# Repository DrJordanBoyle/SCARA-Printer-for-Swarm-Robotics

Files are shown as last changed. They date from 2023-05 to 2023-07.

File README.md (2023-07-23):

# SCARA-Printer-for-Swarm-Robotics
The project explores the development of compact mobile 3D printers inspired by the collective behavior of termites. By mimicking the swarm-like construction techniques employed by termites, this research aims to revolutionize the construction industry through the implementation of innovative robotic systems.
ASS Robotic-Builder_2023-May-10_05-36-22PM-000_CustomizedView9240691610_png_alpha

## Key Points:

1. Termites as Inspiration: Termites exhibit remarkable cooperative behavior in constructing intricate structures without a centralized control unit. Drawing inspiration from this, the project seeks to leverage swarm robotics to enhance construction processes.

2. Compact Mobile 3D Printers: The project has successfully designed and built compact mobile SCARA printers capable of delivering high-quality prints at a relatively high speed. These printers offer the advantage of mobility and flexibility in various construction scenarios.

3. Voxel Printing Strategy: The research introduces a novel voxel printing strategy, simplifying the printing process and increasing efficiency. The proposed strategy has been tested and demonstrated its potential for real-world applications using the SCARA printers.

4. Use Cases and Implications: Swarm 3D printing with SCARA robots holds significant potential in various construction domains. It can streamline building construction, aid in disaster relief efforts by rapidly constructing temporary shelters, and contribute to the expansion and modification of existing structures.

5. The project's findings pave the way for further advancements in swarm robotics and additive manufacturing, providing new possibilities for the construction industry. The research showcases the exciting potential of compact mobile 3D printers and their ability to transform construction processes. This project's outcomes contribute to a safer, more efficient, and sustainable future for the construction sector.

## Navigating the folders:
- In the "Hardware" folder you will find assembly instructions and the .STL files for the 3D printed components.
- In the "Firmware" folder you will find a small log that describes the adjustments made to the standard Marlin firmware and also the custom firmware itself.
- Please use the github in combination with the Thesis paper to fully understand the concept! The thesis 
"Design of a compact and mobile 3D Printer" can be found using the following link: https://repository.tudelft.nl/islandora/object/uuid:e90902cd-7b72-4dd6-bcc3-7ea3ccd2e8e0

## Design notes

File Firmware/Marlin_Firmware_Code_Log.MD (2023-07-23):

# Marlin Code Log

In this segment information is given in regards to what alterations were done to the original Marlin code to have the machine up and running. Good to note is that some changes may have been undocumented. I have tried to add comments to every adjustment, but only wrote them down at the end. It was a long process, you may find an altered line of code that is not documented in this file! You can contact me to update the document. General information on how to work and compile Marlin firmware can be found online. The motherboard we used was generally used to upgrade Creality machines, so some specific adjustments needed to be made. But again, this information can be found online :)

- Marlin version 2.0.9.5
- BTT SKR Mini E3 V3.0 motherboard
- E3D V6 Hot end

## Files that have been altered

- Configuration.h
- scara.cpp

## Configuration.h

- #define MOTHERBOARD BOARD_BTT_SKR_MINI_E3_V3_0 // Line ~90, adjust to own motherboard
- Line ~101 // adjust SERIAL_PORT to your motherboard’s settings
- Line ~114 // adjust BAUDRATE to your motherboard’s baudrate settings
- Line ~154-155 // SCARA_CROSSTALK_FACTOR and SCARA_IS_RIGHT_HANDED variables added to be able to work with different mechanisms. This system does not use an intermediate pulley and is right handed. Its full function can be found in scara.cpp.

#define SCARA_CROSSTALK_FACTOR 1

#define SCARA_IS_RIGHT_HANDED 1

- Line ~157 // define MP_SCARA to be able to use SCARA specific commands and functions
- Line 210-221 // Adjust driver type to the ones your system uses, our motherboard has integrated TMC 2209 drivers.
- Line 562 // Adjust temp_SENSOR_0 to the correct thermistor (we have E3D)
- Line 1098 // Adjust the DEFAULT_AXIS_STEPS_PER_UNIT depending on each stepper’s resolution and micro stepping settings.
- Line 1147-1164 // Some jerk settings were adjusted based on SCARA systems found online
- Line 1590-1601 // Bed dimensions and end stop positions were adjusted. Currently the safe working space is at X = 200 mm and Y = 60 mm. The current home position is set to the corner, but is not used at all in the current operation.

## Scara.cpp

- Line 35 // SCARA_CROSSTALK_FACTOR function added that changes it to 0 if not defined
- Line 56-65 // Forward kinematics were adjusted to include the crosstalk factor, some other older forward kinematics can be found in the file.

```
void forward_kinematics(const_float_t a, const_float_t b) {
  
    const float a_sin = sin(RADIANS(a)) * L1,
                a_cos = cos(RADIANS(a)) * L1,
                b_sin = sin(RADIANS(b + a * SCARA_CROSSTALK_FACTOR)) * L2,
                b_cos = cos(RADIANS(b + a * SCARA_CROSSTALK_FACTOR)) * L2;

    cartes.x = a_cos + b_cos + scara_offset.x;  // theta
    cartes.y = a_sin + b_sin + scara_offset.y;  // phi
```

- Line 172-193 // Some things were adjusted to fine tune the homing settings, but was never tested.
- Line 197 - 218 // Inverse kinematics were added with the SCARA_IS_RIGHT_HANDED and SCARA_CROSSTALK_FACTOR variables integrated into them. More explanation can be found in the code comments. Another line of code was added to see the exact position on the serial monitor.

```cpp
const float x = raw.x - scara_offset.x, y = raw.y - scara_offset.y,             // Finding the desired position, relative to the shoulder location
                hand = SCARA_IS_RIGHT_HANDED ? 1 : -1,                              // Make the SCARA RHS or LHS
                THETA3 = ATAN2(y, x), c2 = HYPOT2(x, y), rc = RSQRT(c2),            // THETA3 is found by simply using inverse tangens with the x and y coordinates of ee           
                THETA1 = THETA3 - hand * ACOS((c2 + sq(L1) - sq(L2)) * rc * RECIPROCAL(2.0f * L1)),   // THETA1 can be found by deducting angle ALFA from THETA3
                THETA2 = THETA3 + hand * ACOS((c2 + sq(L2) - sq(L1)) * rc * RECIPROCAL(2.0f * L2));   // THETA2 is found by deducting

    delta.set(DEGREES(THETA1), DEGREES(THETA2 - THETA1 * SCARA_CROSSTALK_FACTOR), raw.z);   // Sets the THETA1 and THETA2 values in degrees, the SCARA_CROSSTALK_FACTOR is added for non-intermediate pulley systems.

    SERIAL_ECHOLNPGM("  SCARA (x,y) ", x, "   ,  ", y," Theta1=", DEGREES(THETA1), " Theta2=", DEGREES(THETA2));
```

- Line 360-370 // Some more code was added for the serial monitor during setup.

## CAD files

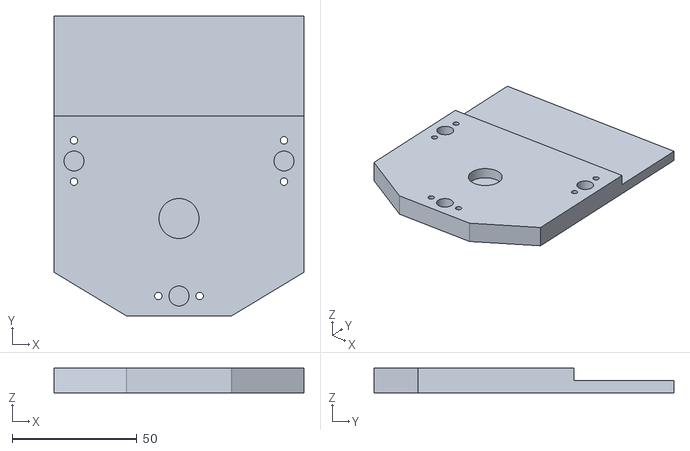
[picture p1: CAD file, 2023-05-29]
Hardware/STL Components/Bottom Base v3.stl
100.0 x 120.0 x 10.0

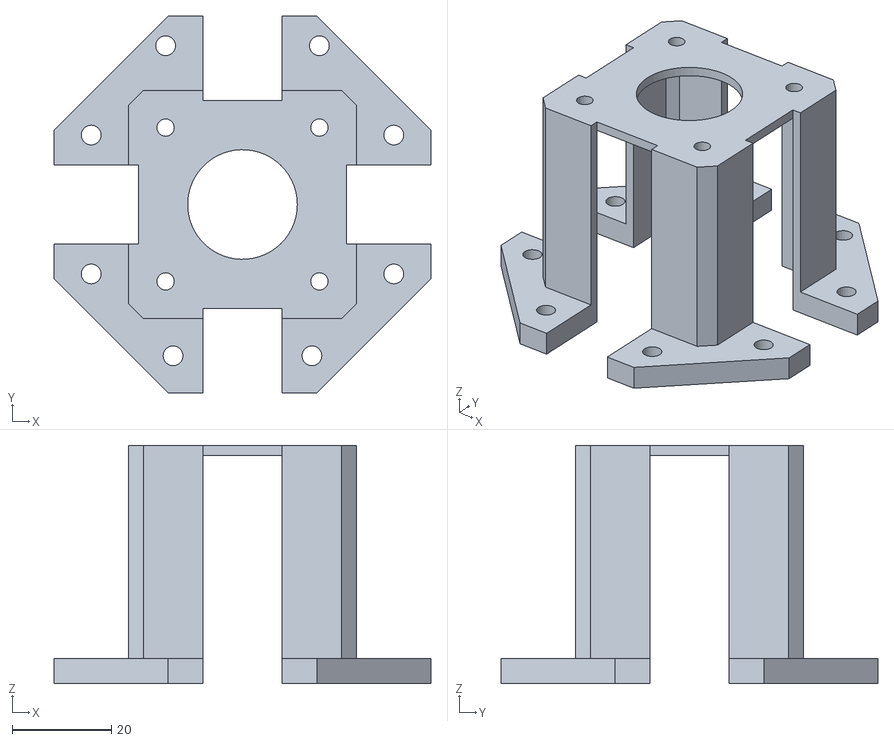
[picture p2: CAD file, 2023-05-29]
Hardware/STL Components/nema17_flange_mount v2.stl
76.0 x 76.0 x 48.0

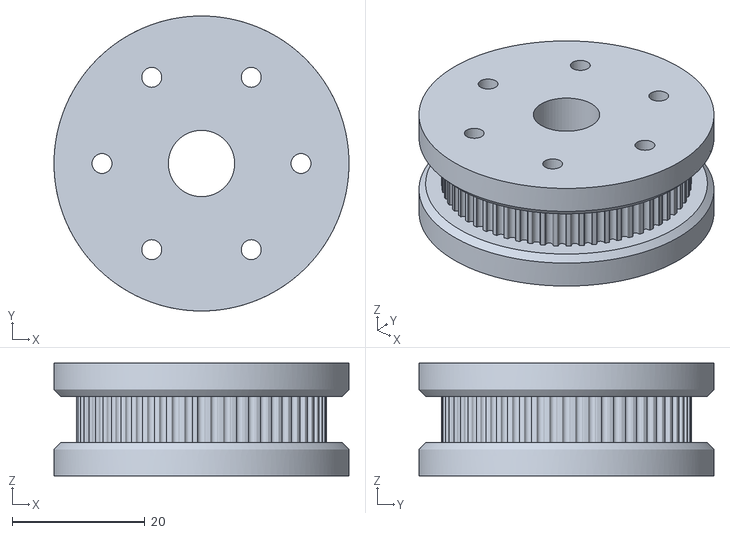
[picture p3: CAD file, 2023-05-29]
Hardware/STL Components/GT2-Custom-ShoulderPulley-N60 v4 v4.stl
44.5 x 44.5 x 17.0

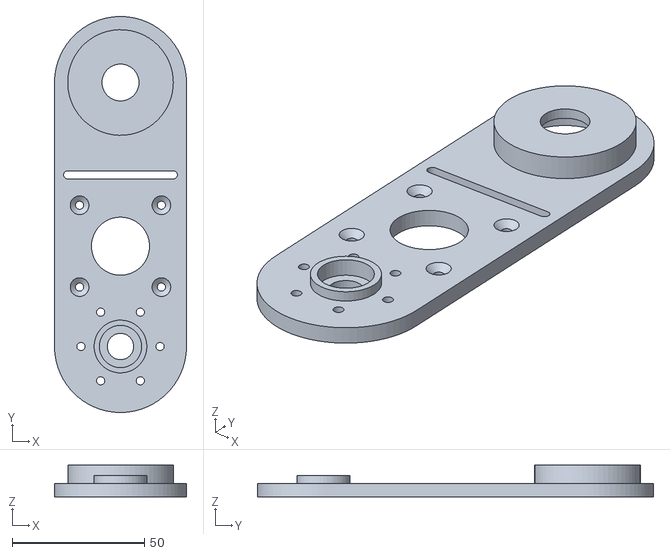
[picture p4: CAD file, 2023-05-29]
Hardware/STL Components/ArmPlate-Bottom(VERS.A) v9.stl
50.0 x 150.0 x 12.0

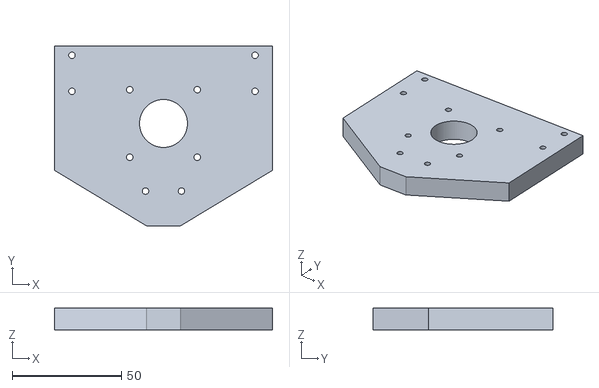
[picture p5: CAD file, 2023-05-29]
Hardware/STL Components/Top Base v3.stl
100.0 x 82.5 x 10.0

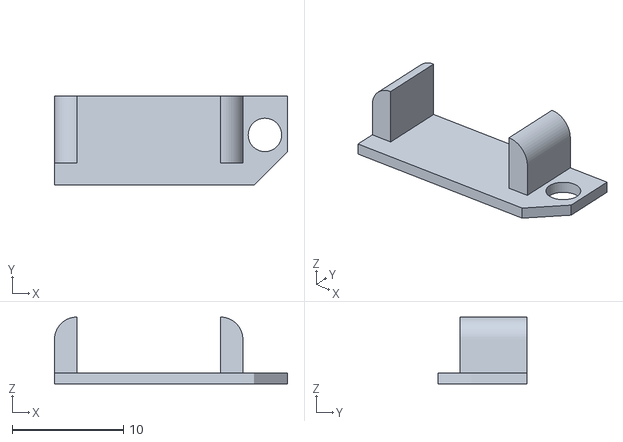
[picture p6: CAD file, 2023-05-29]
Hardware/STL Components/Limit switch holder(ELBOW) v2.stl
20.9 x 8.00 x 6.00

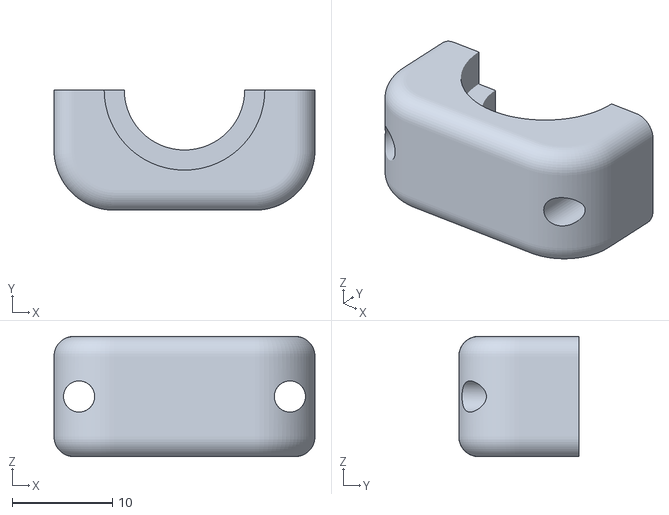
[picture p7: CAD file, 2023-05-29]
Hardware/STL Components/Hot_End_Mount_Front v4.stl
26.0 x 12.0 x 12.0

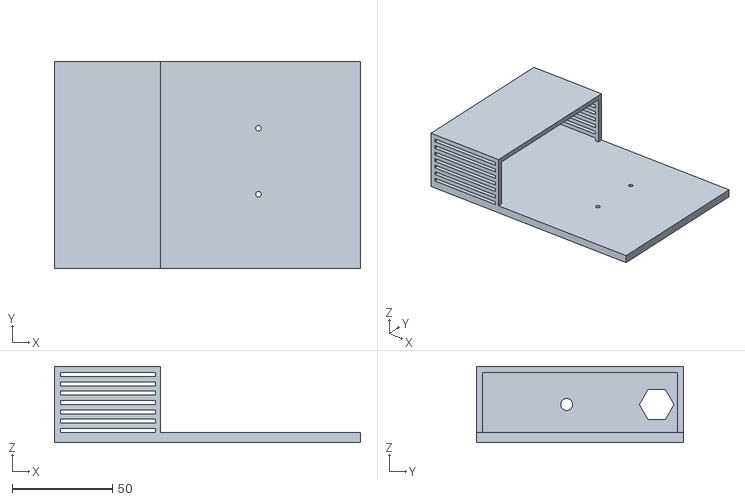
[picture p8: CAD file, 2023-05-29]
Hardware/STL Components/PSU Housing v1.stl
153.0 x 103.3 x 38.0

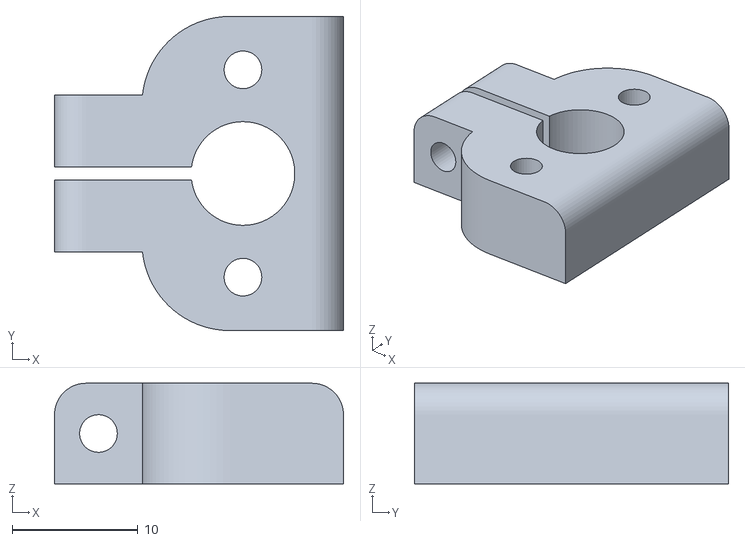
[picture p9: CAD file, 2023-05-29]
Hardware/STL Components/Rod clamp M8 v1.stl
23.0 x 25.0 x 8.00

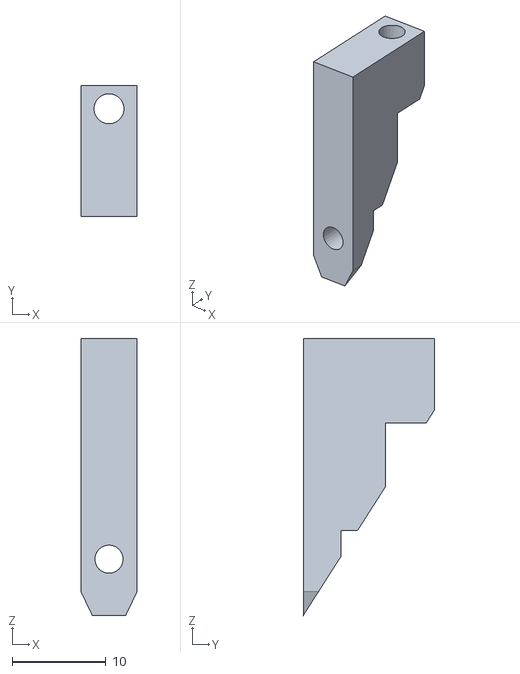
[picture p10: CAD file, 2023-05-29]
Hardware/STL Components/ElbowArm+HotendMount v10.stl
6.00 x 14.0 x 29.5

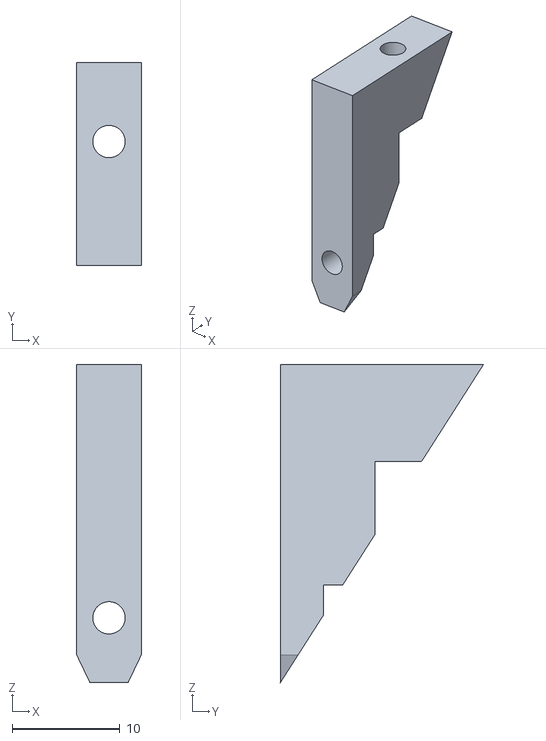
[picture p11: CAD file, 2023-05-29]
Hardware/STL Components/Arm-Mount-Coupler v2.stl
6.00 x 18.8 x 29.5

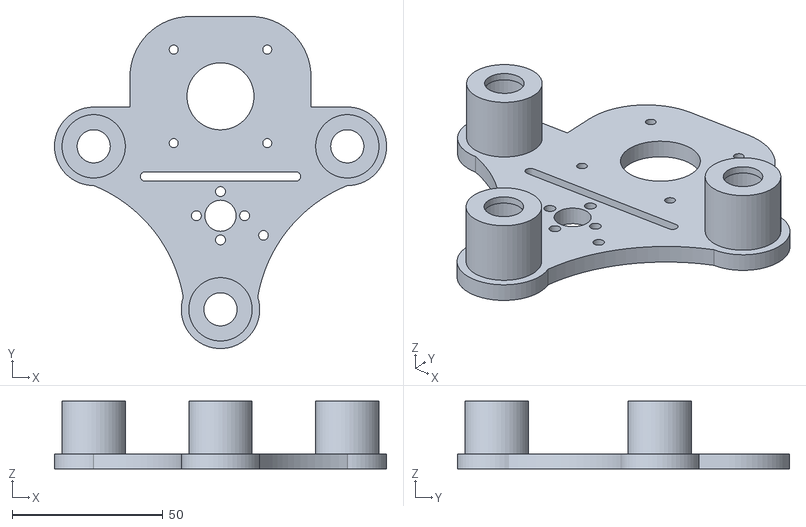
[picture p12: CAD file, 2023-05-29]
Hardware/STL Components/ShoulderPlate_BOTTOM v13.stl
110.0 x 110.0 x 22.5

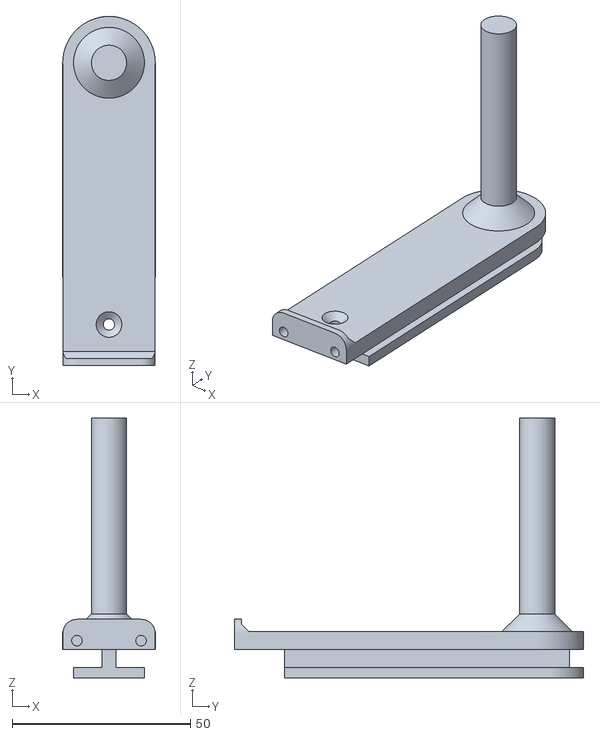
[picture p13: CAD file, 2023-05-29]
Hardware/STL Components/ElbowArm+HotendMount v9.stl
26.0 x 98.0 x 73.0

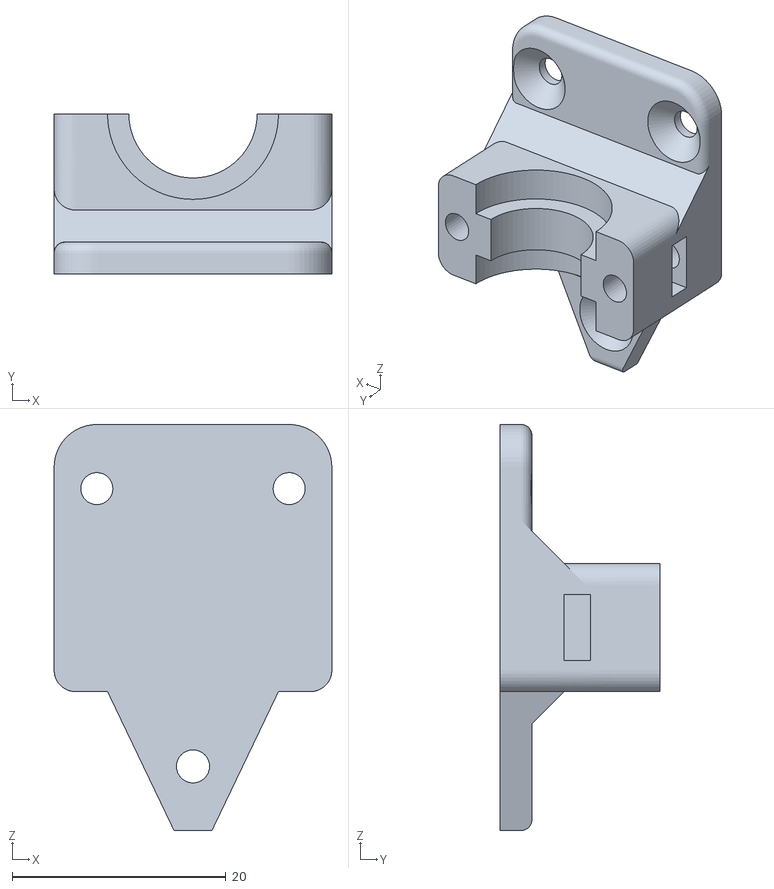
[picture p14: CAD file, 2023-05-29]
Hardware/STL Components/Hot_End_Mount_Backwall v4.stl
26.0 x 15.0 x 38.0

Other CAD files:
Hardware/STL Components/ArmPlate-Top(VERS.A) v9.stl
Hardware/STL Components/GT2-Custom-ElbowPulley-N60 v10.stl
Hardware/STL Components/Limit switch holder (Z) v3.stl

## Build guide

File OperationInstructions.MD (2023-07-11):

# INITIAL INSTRUCTIONS BEFORE PRINTING
The current version of the printer utilizing any limit switches yet, therefore before printing it is necessary to 'home' the system properly by hand. In general the method involves placing the arm at a dinstinct position and using G-CODE to tell the system where its positioned at. From there, the system can function normally.

### Important to note
- The current bed size is set at x-dimension = 60 mm and y-dimension = 200 mm.
- The end effector can move outside of the set bed space, but there is risk of reaching coordinates that are unattainable which will cause malfunctions.
- This project used 'Pronterface' to connect and interact with the printer using a computer, there are other softwares that do the same.

### Initial settings
1. Use G-CODE M906 to limit the current for the steppers for the X and Y to 850 mA while the extruder stepper can be set to 1000 mA. In the serial monitor you can insert "M906 X850 Y850 Z850 E1000".
2. Use G-code M500 to save settings in the EPROM.

### Step by step instructions
1. Connect the motherboard with a computer with Pronterface using the given USB cable (micro USB probably).

2. Make sure you are using the correct port by selecting the port on the top left, and also make sure the baudrate is set to the correct value which can be found next to the port settings. In this case, using the BTT SKR Mini E3 the baudrate should be set to 115200.

Pronterface interface

3. On the top left, you can press connect and a message should pop up in the serial monitor on the right side that says "Printer is now online.".

4. Place the arms/links straight out in front of the machine, making sure that the angles theta1 and theta2 are 90 degrees (or as near as possible).

How to initially setup the links

5. Using an interface such as Pronterface, use G-CODE G92 to indicate the current position. Fill out "G92 X50 Y109.5". This position was calculated as the coordinates of the end effector when theta1 and theta2 are 90 degrees. If your system differs in any way in the physical dimensions these coordinates must be recalculated.

6. From here, you should be able to use G-CODE G1 to move around the end effector. The center of this print area can be found at (30,100). Use "G1 X30 Y100" to move the end effector to the middle of the 'bed'.

7. Now the Z-axis position must be homed, using the interface on pronterface keep moving the z-axis down until the hot-end is near the surface. Use a piece of A4 paper and place it between the hot end and the surface, you want to be able to move the paper around freely with some minor resistance. When that point is found, use "G92 Z0" to indicate the positioning of the Z-Axis.

### 8. IMPORTANT: Turn on the fan manually and set to 100% before printing! Use "M106 P2 S255" to set the hot end fan to 100%. The S indicates the power with 255 being 100%, the P indicates the fan index, could vary if a different setup is used. Withot this the hot end holder may start to deform due to the heat.

9. You can now start printing!

# Operational Instructions
The printer is quite barebones at this point, meaning that various things still must be done manually. Here below you will find general steps to take during printing.

1. Good to do before printing is to pre heat the hot end and extrude a bit of the filament to double check that everything is set correctly, if the filament exits the nozzle in a somewhat straight line to the surface the printer is ready.

2. Upon inserting the G-Code file Pronterface will show a mockup of the 3D model. In the top section of the interface you will find the print button, when pressed the system will start to pre-heat the hot end and finally print.

3. At the end of the print it does not have the correct commands installed yet to end the print, so at the very last coordinate it will stop in place. To remove the nozzle from the print one must reset the printer and use the jog commands (the arrows in pronterface) to quickly remove the nozzle from the print.

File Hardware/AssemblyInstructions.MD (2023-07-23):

# Assembly instructions SCARA ARM

## General components overview






## Part 1: Assemble the Tower

Consists of the base, top plate, x2 shoulder plates (top and bottom).

### Preparing the base, top plate and shoulder plates

- Begin by placing the base on a flat surface and securely attach the rod clamps using M3 bolts and nuts. The base is designed with compartments on the bottom to accommodate the nuts conveniently.
    
SCARAPRINTER_VERS A v25
    
- Next, carefully insert the three smooth rods into the attached rod clamps on the bottom base. Use another set of M3 bolts and nuts to secure the rods in place. Ensure the rods are aligned properly for smooth movement and stability.
    
SCARAPRINTER_VERS A v251
    
- To begin assembling the top plate/lid, mount the rod clamps onto the plate using M3x16mm bolts, similar to the process used for the base. Place the rod clamps on the face of the plate that is facing towards the base/ground. Make sure to fasten the bolts securely to ensure stability and proper alignment.
- Next, attach the Z-stepper onto the top plate, positioning the shaft towards the ground, just like the rod clamps. Securely fasten the stepper using four M3x16mm nuts and bolts. Double-check the alignment and tighten the nuts and bolts to ensure a stable and reliable connection. This step is crucial for the proper functioning of the printer's vertical movement.
- Attach the Z-coupler to the Z-stepper shaft using the provided bolts. Then, connect the leadscrew to the coupler to complete the assembly of the top plate. Handle it with care, as it plays a crucial role in the printer's precise vertical movement.
    
SCARAPRINTER_VERS A v25234
    
- Begin with the bottom shoulder plate. Insert the three linear bearings (8x15x24) into the designated compartments, ensuring they protrude slightly when fully inserted. Use a rubber hammer for secure fitting; note that this is a permanent installation. Next, attach the lead screw coupler to the plate using M3 bolts and nuts. Ensure the protrusion faces downward for proper functionality.

SCARAPRINTER_VERS A v253

- Similar to the bottom shoulder plate, prepare the top shoulder plate by inserting the three linear bearings and attaching the lead screw coupler using M3 bolts and nuts. Ensure that the components are securely in place.Partially fasten the stepper motor on the top plate using 2 x M3 nuts and bolts. Use the inner two holes for this step, leaving the two holes near the edge of the plate free for later adjustments and additional components.

SCARAPRINTER_VERS A v254

### Assembling Tower

- Carefully slide the bottom shoulder plate onto the three rods, ensuring that the open-faced bearings are pointing towards the sky. Take your time to align the rods properly before sliding on the bottom shoulder plate. This precaution is essential to avoid any damage to the inner walls of the linear bearings.
- The rest of the assembly can only be done after preparing the arm.

SCARAPRINTER_VERS A v255
## Part 2: Assemble the arm

Consists of the elbow link and shoulder link.

### Preparing the shoulder link

- Prepare the shoulder link (plates) by inserting the bearings. On the end that connects to the shoulder plates, there are two compartments on the top and bottom faces of the shoulder plates. Insert two 8x16mm thrust bearings into these compartments. Ensure that the bearings are form-fitted into the compartments securely.

SCARAPRINTER_VERS A v256

- On the other end, there are two compartments again, but this time they can be found on the inside faces of the two plates. Here, you can fit the two angular bearings. The sizes of the angular bearings and thrust bearings are quite different, so there is no way of placing them incorrectly. Ensure that these bearings are inserted all the way in, especially the angular ones, to ensure a secure fit.

SCARAPRINTER_VERS A v257

- Prepare the shoulder arm/link by placing the custom pulleys between the top and bottom shoulder arm plates. Ensure that the pulleys are "sandwiched" by the two shoulder link plates. Position the pulley with no holes on its sides towards the base (where the thrust bearings are located), while the pulley with horizontal holes should be placed towards the end effector (where the angular bearings are). Please note that the latter pulley will only be positioned there for now and not secured yet.
    
SCARAPRINTER_VERS A v258
    
- Before securing the pulley near the base, make sure to place the GT2 belt (the longer one) around the pulley while it is positioned between the two shoulder link plates. It's essential to do this before locking the pulley in place, as there won't be a way to place the GT2 belt there afterward. Take care to position the belt properly during this step.
- To secure the pulley near the base, use x6 M3x20 bolts and nuts. Drive them through the two shoulder link plates and the pulley itself, fastening everything together tightly. This will ensure the pulley is securely attached between the plates.
- Position the second stepper motor in the middle of the shoulder link, aligning it with the four holes on each plate. Note that four of these holes have a chamfered side, which should face the ground. The stepper motor's shaft should pass through the hole, pointing towards the bottom plate. Use x4 M3x30 nuts and bolts to secure the stepper motor in place, pushing the bolts through both sets of holes to strengthen the double plate setup. With the stepper motor and custom pulley installed, your shoulder link will become significantly sturdier.
    
SCARAPRINTER_VERS A v2599

### Assembling the Tower / Arm

- Slide the fully assembled shoulder link onto the smooth rod located in the middle. The thrust bearing in the shoulder link should rest on top of the linear bearing that is secured on the bottom shoulder plate. This arrangement will allow for smooth movement and stability in the shoulder assembly.
- Slide the fully assembled top shoulder plate onto the three smooth rods, taking care to avoid scratching the inside of the linear bearings. Ensure that the protrusion from the compartments for the linear bearings points upward for proper functioning and smooth motion of the shoulder assembly.
- You now have a sandwich with the shoulder link in between the two shoulder plates.

SCARAPRINTER_VERS A v25894

- Secure the installed components using the lead screw attached to the lid plate. Insert the lead screw through the couplers on the top and bottom shoulder plates and slowly turn it until the lid reaches the top of the smooth rods. Fasten the smooth rods into the rod clamps on the top/lid to fix the distance between the top and bottom shoulder plates. This ensures stability and proper alignment of the shoulder assembly.
- With the fixed distance, complete the installation of the shoulder stepper by using 2 M3x30 bolts and nuts through both the bottom and top shoulder plates. This double-layer setup adds reinforcement to the assembly, ensuring the shoulder stepper is securely in place.

SCARAPRINTER_VERS A v25546

### Preparing the Elbow link and final arm assembly

- You can now start preparing the final link, the elbow link which consists of the link itself, the hot end mount and the hot end.
- Attach the elbow link to the hot end mount with two M3x16 bolts, after which you can place the little coupler piece that reinforces the connection between the link and mount. This little coupler uses two M3x10 bolts.
- Attach the partly assembled elbow link to the shoulder link. The elbow link features a cylindrical protrusion that fits into the holes at the end of the shoulder link. Before inserting the protrusion, ensure that the second custom pulley is placed between the two shoulder link plates, along with the second GT2 belt (the shorter one) positioned on the pulley.
- Once the pulley and belt are in place, insert the protrusion through the three layers. Secure the assembly by using 8 headless bolts, screwing them horizontally into the custom pulley to lock the protrusion in place. While the height to lock in the elbow link is flexible, it is recommended not to position it too far below the shoulder link to minimize stress points in the protrusion.

SCARAPRINTER_VERS A v25874221

- Lastly, attach the hot end to its mount using 2x M3x16 nuts and bolts. Insert the nuts into their respective compartments from the side to create a self-locking system. By screwing in the bolts, the hot end will tighten itself securely in place.

SCARAPRINTER_VERS A v255645

## Part 3: Final touches

- The extruder stepper can be inserted into the mount and then attached to base plate on the back end by using some nuts and bolts.
- Now the idler pulleys can be installed, there are a total of 2 idler pulley rods which are placed on the elbow link and the shoulder plates. To setup the idler pulleys, you use threaded ends in which the idler pulley is placed in the middle of the threaded ends. It is fixed by using two nuts with a spring ring placed between the nut and idler pulley, tighten to fix the pulley. Both the idler rods are then fixed into the slots by using a ring, spring ring and nuts to tighten it in place, make sure the belt is tensioned enough by sliding the rod in the slot.

SCARAPRINTER_VERS A v258948945

- There are small mounts designed to house the limit switches, you can attach one on the lead screw coupler, the second has no attachment point yet. These limit switches are not integrated into the firmware yet as of time of writing.
- A spool holder, limit switches and filament line holder are not added yet but are advisable to design.

## NOTE
- For the hot end assembly please follow the guide of E3D that you can find online. The temperature settings must be adjusted first to correctly install the hot end.

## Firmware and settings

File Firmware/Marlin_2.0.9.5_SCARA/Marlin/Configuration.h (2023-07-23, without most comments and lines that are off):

#pragma once
#define CONFIGURATION_H_VERSION 02000905
#define STRING_CONFIG_H_AUTHOR "(none, default config)" // Who made the changes.
#define SHOW_BOOTSCREEN
  #define MOTHERBOARD BOARD_BTT_SKR_MINI_E3_V3_0
#define SERIAL_PORT -1
#define BAUDRATE 115200
#define CUSTOM_MACHINE_NAME "DEKU SCARA BUILD V2.0"
#define SCARA_CROSSTALK_FACTOR 1    // Change value depending on your mechanism, we do not use an intermediate pulley
#define SCARA_IS_RIGHT_HANDED 1     // Change value depending on having an RHS or LHS system, RHS =1, LHS = -1
#define MP_SCARA
  #define SCARA_SEGMENTS_PER_SECOND 200
  #define SCARA_LINKAGE_1 100       // (mm)
  #define SCARA_LINKAGE_2 100       // (mm)
  #define SCARA_OFFSET_X   100     // (mm) BUILDPLATE of 200 x 60
  #define SCARA_OFFSET_Y  -112.5      // (mm)
    #define SCARA_OFFSET_THETA1  12 // degrees
    #define SCARA_OFFSET_THETA2 131 // degrees
#define X_DRIVER_TYPE  TMC2209
#define Y_DRIVER_TYPE  TMC2209
#define Z_DRIVER_TYPE  TMC2209
#define E0_DRIVER_TYPE TMC2209
#define EXTRUDERS 1
#define DEFAULT_NOMINAL_FILAMENT_DIA 1.75
#define TEMP_SENSOR_0 5
#define TEMP_SENSOR_1 0
#define TEMP_SENSOR_2 0
#define TEMP_SENSOR_3 0
#define TEMP_SENSOR_4 0
#define TEMP_SENSOR_5 0
#define TEMP_SENSOR_6 0
#define TEMP_SENSOR_7 0
#define TEMP_SENSOR_BED 0
#define TEMP_SENSOR_PROBE 0
#define TEMP_SENSOR_CHAMBER 0
#define TEMP_SENSOR_COOLER 0
#define TEMP_SENSOR_BOARD 0
#define TEMP_SENSOR_REDUNDANT 0
#define DUMMY_THERMISTOR_998_VALUE  25
#define DUMMY_THERMISTOR_999_VALUE 100
#define TEMP_RESIDENCY_TIME         10  // (seconds) Time to wait for hotend to "settle" in M109
#define TEMP_WINDOW                  1  // (°C) Temperature proximity for the "temperature reached" timer
#define TEMP_HYSTERESIS              3  // (°C) Temperature proximity considered "close enough" to the target
#define TEMP_BED_RESIDENCY_TIME     10  // (seconds) Time to wait for bed to "settle" in M190
#define TEMP_BED_WINDOW              1  // (°C) Temperature proximity for the "temperature reached" timer
#define TEMP_BED_HYSTERESIS          3  // (°C) Temperature proximity considered "close enough" to the target
#define TEMP_CHAMBER_RESIDENCY_TIME 10  // (seconds) Time to wait for chamber to "settle" in M191
#define TEMP_CHAMBER_WINDOW          1  // (°C) Temperature proximity for the "temperature reached" timer
#define TEMP_CHAMBER_HYSTERESIS      3  // (°C) Temperature proximity considered "close enough" to the target
#if TEMP_SENSOR_REDUNDANT
  #define TEMP_SENSOR_REDUNDANT_SOURCE    E1  // The sensor that will provide the redundant reading.
  #define TEMP_SENSOR_REDUNDANT_TARGET    E0  // The sensor that we are providing a redundant reading for.
  #define TEMP_SENSOR_REDUNDANT_MAX_DIFF  10  // (°C) Temperature difference that will trigger a print abort.
#endif
#define HEATER_0_MINTEMP   5
#define HEATER_1_MINTEMP   5
#define HEATER_2_MINTEMP   5
#define HEATER_3_MINTEMP   5
#define HEATER_4_MINTEMP   5
#define HEATER_5_MINTEMP   5
#define HEATER_6_MINTEMP   5
#define HEATER_7_MINTEMP   5
#define BED_MINTEMP        5
#define CHAMBER_MINTEMP    5
#define HEATER_0_MAXTEMP 275
#define HEATER_1_MAXTEMP 275
#define HEATER_2_MAXTEMP 275
#define HEATER_3_MAXTEMP 275
#define HEATER_4_MAXTEMP 275
#define HEATER_5_MAXTEMP 275
#define HEATER_6_MAXTEMP 275
#define HEATER_7_MAXTEMP 275
#define BED_MAXTEMP      150
#define CHAMBER_MAXTEMP  60
#define HOTEND_OVERSHOOT 15   // (°C) Forbid temperatures over MAXTEMP - OVERSHOOT
#define BED_OVERSHOOT    10   // (°C) Forbid temperatures over MAXTEMP - OVERSHOOT
#define COOLER_OVERSHOOT  2   // (°C) Forbid temperatures closer than OVERSHOOT
#define PIDTEMP          // See the PID Tuning Guide at https://reprap.org/wiki/PID_Tuning
#define BANG_MAX 255     // Limits current to nozzle while in bang-bang mode; 255=full current
#define PID_MAX BANG_MAX // Limits current to nozzle while PID is active (see PID_FUNCTIONAL_RANGE below); 255=full current
#define PID_K1 0.95      // Smoothing factor within any PID loop
    #define DEFAULT_Kp  22.20
    #define DEFAULT_Ki   1.08
    #define DEFAULT_Kd 114.00
#define MAX_BED_POWER 255 // limits duty cycle to bed; 255=full current
#define MAX_CHAMBER_POWER 255 // limits duty cycle to chamber heater; 255=full current
  #define PID_FUNCTIONAL_RANGE 10 // If the temperature difference between the target temperature and the actual temperature
#define PREVENT_COLD_EXTRUSION
#define EXTRUDE_MINTEMP 170
#define PREVENT_LENGTHY_EXTRUDE
#define EXTRUDE_MAXLENGTH 200
#define THERMAL_PROTECTION_HOTENDS // Enable thermal protection for all extruders
#define THERMAL_PROTECTION_BED     // Enable thermal protection for the heated bed
#define THERMAL_PROTECTION_CHAMBER // Enable thermal protection for the heated chamber
#define THERMAL_PROTECTION_COOLER  // Enable thermal protection for the laser cooling
#define USE_XMIN_PLUG
#define USE_YMIN_PLUG
#define USE_ZMIN_PLUG
#define ENDSTOPPULLUPS
#define X_MIN_ENDSTOP_INVERTING false // Set to true to invert the logic of the endstop.
#define Y_MIN_ENDSTOP_INVERTING false // Set to true to invert the logic of the endstop.
#define Z_MIN_ENDSTOP_INVERTING false // Set to true to invert the logic of the endstop.
#define I_MIN_ENDSTOP_INVERTING false // Set to true to invert the logic of the endstop.
#define J_MIN_ENDSTOP_INVERTING false // Set to true to invert the logic of the endstop.
#define K_MIN_ENDSTOP_INVERTING false // Set to true to invert the logic of the endstop.
#define X_MAX_ENDSTOP_INVERTING false // Set to true to invert the logic of the endstop.
#define Y_MAX_ENDSTOP_INVERTING false // Set to true to invert the logic of the endstop.
#define Z_MAX_ENDSTOP_INVERTING false // Set to true to invert the logic of the endstop.
#define I_MAX_ENDSTOP_INVERTING false // Set to true to invert the logic of the endstop.
#define J_MAX_ENDSTOP_INVERTING false // Set to true to invert the logic of the endstop.
#define K_MAX_ENDSTOP_INVERTING false // Set to true to invert the logic of the endstop.
#define Z_MIN_PROBE_ENDSTOP_INVERTING false // Set to true to invert the logic of the probe.
#define DEFAULT_AXIS_STEPS_PER_UNIT   { 26.6667, 26.6667, 400, 93 } // With new nema 17 stepper
#define DEFAULT_MAX_FEEDRATE          { 300, 300, 5, 25 }
#define DEFAULT_MAX_ACCELERATION      { 3000, 3000, 100, 10000 }
#define DEFAULT_ACCELERATION          3000    // X, Y, Z ... and E acceleration for printing moves
#define DEFAULT_RETRACT_ACCELERATION  3000    // E acceleration for retracts
#define DEFAULT_TRAVEL_ACCELERATION   3000    // X, Y, Z ... acceleration for travel (non printing) moves
#define CLASSIC_JERK
  #define DEFAULT_XJERK 5.0
  #define DEFAULT_YJERK 5.0
  #define DEFAULT_ZJERK  0.3
#define DEFAULT_EJERK    5.0  // May be used by Linear Advance
#define Z_MIN_PROBE_USES_Z_MIN_ENDSTOP_PIN
#define NOZZLE_TO_PROBE_OFFSET { 10, 10, 0 }
#define PROBING_MARGIN 10
#define XY_PROBE_FEEDRATE (133*60)
#define Z_PROBE_FEEDRATE_FAST (4*60)
#define Z_PROBE_FEEDRATE_SLOW (Z_PROBE_FEEDRATE_FAST / 2)
#define Z_CLEARANCE_DEPLOY_PROBE   10 // Z Clearance for Deploy/Stow
#define Z_CLEARANCE_BETWEEN_PROBES  5 // Z Clearance between probe points
#define Z_CLEARANCE_MULTI_PROBE     5 // Z Clearance between multiple probes
#define Z_PROBE_LOW_POINT          -2 // Farthest distance below the trigger-point to go before stopping
#define Z_PROBE_OFFSET_RANGE_MIN -20
#define Z_PROBE_OFFSET_RANGE_MAX 20
#define X_ENABLE_ON 0
#define Y_ENABLE_ON 0
#define Z_ENABLE_ON 0
#define E_ENABLE_ON 0 // For all extruders
#define DISABLE_X false
#define DISABLE_Y false
#define DISABLE_Z false
#define DISABLE_E false             // Disable the extruder when not stepping
#define DISABLE_INACTIVE_EXTRUDER   // Keep only the active extruder enabled
#define INVERT_X_DIR false
#define INVERT_Y_DIR true
#define INVERT_Z_DIR false
#define INVERT_E0_DIR false
#define INVERT_E1_DIR false
#define INVERT_E2_DIR false
#define INVERT_E3_DIR false
#define INVERT_E4_DIR false
#define INVERT_E5_DIR false
#define INVERT_E6_DIR false
#define INVERT_E7_DIR false
#define X_HOME_DIR -1
#define Y_HOME_DIR -1
#define Z_HOME_DIR -1
#define X_BED_SIZE 200
#define Y_BED_SIZE 60
#define X_MIN_POS (0-X_BED_SIZE/2)
#define Y_MIN_POS (0-Y_BED_SIZE/2)
#define Z_MIN_POS 0
#define X_MAX_POS (X_BED_SIZE/2)
#define Y_MAX_POS (Y_BED_SIZE/2)
#define Z_MAX_POS 200
#define MIN_SOFTWARE_ENDSTOPS
  #define MIN_SOFTWARE_ENDSTOP_X
  #define MIN_SOFTWARE_ENDSTOP_Y
  #define MIN_SOFTWARE_ENDSTOP_Z
  #define MIN_SOFTWARE_ENDSTOP_I
  #define MIN_SOFTWARE_ENDSTOP_J
  #define MIN_SOFTWARE_ENDSTOP_K
#define MAX_SOFTWARE_ENDSTOPS
  #define MAX_SOFTWARE_ENDSTOP_X
  #define MAX_SOFTWARE_ENDSTOP_Y
  #define MAX_SOFTWARE_ENDSTOP_Z
  #define MAX_SOFTWARE_ENDSTOP_I
  #define MAX_SOFTWARE_ENDSTOP_J
  #define MAX_SOFTWARE_ENDSTOP_K
#define HOMING_FEEDRATE_MM_M { (50*60), (50*60), (4*60) }
#define VALIDATE_HOMING_ENDSTOPS
#define EEPROM_SETTINGS     // Persistent storage with M500 and M501
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

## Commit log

2023-07-23 Rename Marlin_Log.MD to Marlin_Firmware_Code_Log.MD
    General overview of the adjustments made to the existing Marlin code for this system. More information can be found in the code itself.
2023-07-23 Added all files
    [Arm-Mount-Coupler v2.stl, ArmPlate-Bottom(VERS.A) v9.stl, ArmPlate-Top(VERS.A) v9.stl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]
2023-07-23 added new one again.
    [Configuration.h, Configuration_adv.h, esp32.csv]

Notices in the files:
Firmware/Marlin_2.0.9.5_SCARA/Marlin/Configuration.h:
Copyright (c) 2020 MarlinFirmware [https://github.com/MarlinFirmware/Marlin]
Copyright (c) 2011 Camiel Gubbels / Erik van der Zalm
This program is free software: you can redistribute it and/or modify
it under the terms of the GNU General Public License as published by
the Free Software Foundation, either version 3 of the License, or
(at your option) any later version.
